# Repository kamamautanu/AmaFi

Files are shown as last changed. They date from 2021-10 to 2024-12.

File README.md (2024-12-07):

# AmaFi
Automated water-wise irrigation system

As someone new to the world of engineering, a friend encouraged me to create something that would make life easier for me. Something like automating watering in my garden so I don't spend 6 or more hours a week doing it by hand during the heat of summer. Initially, I resisted the idea of integrating technology into my gardening space, but as spring turned into summer and the hot California sun blasted my garden full force, what had once been a labor of love quickly turned into feelings of frustration at both the amount of time I spent watering and the amount of water I was using during a "mega-drought".

Water scarcity isn't an issue of the future, it's happening right here and now. Enter the AmaFi. The AmaFi only applies water where plants need it and when. No more worrying about over or under watering, the AmaFi takes out the guess work in growing drought resiliant gardens while conserving water compared to conventional methods. The AmaFi does this by integrating a number of gardening theories and features:
  * [deep watering]() - water less often for longer for deeper moisture penetration
  * [drip irrigation]() - reduces evapotranspiration, plant disease, and efficiently waters deeply
  * [irrigation zones] - three watering zones for crops based on rooting depth categories - low, medium, high.

# Table of Contents

  [What is AmaFi?](https://github.com/kamamautanu/AmaFi/blob/main/README.md#what-is-amafi)
  
  [What is next for AmaFi?](https://github.com/kamamautanu/AmaFi/blob/main/README.md#what-is-next-for-amafi)

Component Details
  1.  [Microprocessor](https://github.com/kamamautanu/AmaFi/blob/main/README.md#1-microprocessor)
  2.  [Case](https://github.com/kamamautanu/AmaFi/blob/main/README.md#2-case)
  3.  [Soil Moisture Sensor](https://github.com/kamamautanu/AmaFi/blob/main/README.md#3-soil-moisture-sensor)
  4.  [Relay](https://github.com/kamamautanu/AmaFi/blob/main/README.md#4-relay)
  5.  [Solenoid Valve](https://github.com/kamamautanu/AmaFi/blob/main/README.md#5-solenoid-valve)
  6.  [I2C Multiplexer](https://github.com/kamamautanu/AmaFi/blob/main/README.md#6-i2c-multiplexer)
  7.  [Other electrical components](https://github.com/kamamautanu/AmaFi/blob/main/README.md#7-other-electrical-components)
  8.  [Backflow Preventer](https://github.com/kamamautanu/AmaFi/blob/main/README.md#8-backflow-preventer)
  9.  [Water Pressure Regulator](https://github.com/kamamautanu/AmaFi/blob/main/README.md#9-water-pressure-regulator)
  10. [Water Filter](https://github.com/kamamautanu/AmaFi/blob/main/README.md#10-water-filter)
  11. [PVC Components](https://github.com/kamamautanu/AmaFi/blob/main/README.md#11-pvc-components)
  12. [Valves](https://github.com/kamamautanu/AmaFi/blob/main/README.md#12-valves)
  13. [Mainline](https://github.com/kamamautanu/AmaFi/blob/main/README.md#13-mainline)
  14. [Connecctors](https://github.com/kamamautanu/AmaFi/blob/main/README.md#14-Connectors)
  15. [Dripline](https://github.com/kamamautanu/AmaFi/blob/main/README.md#15-dripline)
  16. [Plugs and Caps](https://github.com/kamamautanu/AmaFi/blob/main/README.md#16-plugs-and-caps)
  17. [Other irrigation components](https://github.com/kamamautanu/AmaFi/blob/main/README.md#17-other-irrigation-components)  

[Bill of Materials (BOM)](https://github.com/kamamautanu/AmaFi/blob/main/README.md#bill-of-materials-BOM)

[Firmware](https://github.com/kamamautanu/AmaFi/blob/main/README.md#firmware)

[Schematic](https://github.com/kamamautanu/AmaFi/blob/main/README.md#schematic)

[User Manual](https://github.com/kamamautanu/AmaFi/blob/main/README.md#user-manual)

[FAQs](https://github.com/kamamautanu/AmaFi/blob/main/README.md#faqs)

[Tech Details](https://github.com/kamamautanu/AmaFi/blob/main/README.md#tech-details)

[Known Bugs](https://github.com/kamamautanu/AmaFi/blob/main/README.md#known-bugs)

[License](https://github.com/kamamautanu/AmaFi/blob/main/README.md#license)

# What is AmaFi?

I was inspired to create AmaFi to reduce the amount of time and water required by my garden. Ama, or more properly ᎠᎹ, is the Cherokee word for water and my watering system is powered by WiFi. How cool is that!

# What is next for AmaFi?

Four words - going solar and wireless. That's right, now that I have a functioning system up and running I can focus on making improvements. Check out some of my PCB designs in the making to improve the soil moisture sensors by trying to maximize parasitic capacitance. 

# Component Details

## 1. Microprocessor

The AmaFi uses the common microprocessor Raspberry Pi Zero W. It's compact, inexpensive, and has more than enough capacity and power for the AmaFi system.

Any Raspberry Pi requires a formatted microSD card and with hundreds of them on the market, the decision paralysis can set in quickly. The AmaFi is housed outdoors and while several weatherproofing techniques are used, the long-term performance of a microSD card is another critical factor in choosing one. With this in mind, I did some research to find a card with plenty of memory that was best for long-term performance and would perform *well enough* on the RasPi Zero W. My research led my to choose a 32GB Samsung Pro Endurance. It doesn't seem that anyone actually knows whether this microSD card lives up to the claims yet, but I figured it was worth a shot for starters. For more information about choosing a microSD for the RasPi, I found [this post](https://www.tomshardware.com/best-picks/raspberry-pi-microsd-cards) to be a good resource.

The microUSB port on the RasPi Zero W powers the system through a DC adapter plugged into a power outlet. Some of the other RasPi Zero W features utilized in this project are built in WiFi configured using headless setup, the I2C Interface, both the 3.3V and 5V power rails, digital pins that can be pulled high, among others.

## 2. Case

Since the electronic components of this system are located outdoors, thorough weatherproofing is especially imperative to the longevity of the device. With this in mind, a 3D enclosure was designed in OpenSCAD and Cura was used to convert the model into 3D printable g-code. The enclosure features 2 supports with zip tie slots, 2 internal pegs to mount 2 [half-sized Adafruit Permaboards](https://www.adafruit.com/product/571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), and a removable bottom that has 6 - 1/2 inch cylindrical cutouts for wires and a polygoon cutout for power adapters. The details for the AmaFi enclosure can be found [here](https://github.com/kamamautanu/AmaFi/tree/main/case). 

## 3. Soil Moisture Sensor

Soil moisture sensors use either resistive or capacitive sensing. Resistive sensors impute the volumentric content of water by measuring the current that passes through the soil between the two sensor prongs to get a resistance value. By design resistive sensors corrode quickly as current runs through the exposed soil probes causing electrolysis. On the other hand, capacitive sensing measures the dielectic formed by the soil and is actually a more accurate measure of soil moisture content compared to resistive sensing. Something like applying fertilizer would decrease the resistance sensor reading, but the most important factor influencing dielectic measurements taken by capacitance sensors is water. Capacitive sensors themselves are made out of a more corrossion resistive material, meaning they last longer than metal resistive sensors. I chose to go with the [Adafruit Capacitive Soil Moisture Sensor](https://www.adafruit.com/product/4026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). It runs on the I2C Bus, uses the MIT license, and comes with the added bonus of a temperature sensor that is accurate to +/- 2 degrees Celcius, which is good enough for my purposes.     

## 4. I2C Multiplexer

The Inter-Integrated Circuit (I2C) Interface on the Raspberry Pi allows multiple I2C devices to be connected to one I2C Bus as long as each device has a unique I2C address - multiple instances of the same address are not allowed. An I2C multiplexer allows multiple I2C sensors with the same I2C address to be connected to different channels on the multiplexer, thus allowing multiple sensors with the same I2C address to connect to one I2C Bus. One multiplexer was plenty for the 6 soil moisture sensors I needed to connect, but it is possible to implement more. I chose the [TCA9548A I2C Multiplexer](https://www.adafruit.com/product/2717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) from Adafruit.

## 5. Relay

In order to create three irrigation zones that operated and could be water idependently of one another, I had to utilize three relays. These relays run on digital GPIO pins that can be pulled high on the Raspberry Pi. Continuing the open source theme, I used the [Adafruit STEMMA Non-Latching Mini Relay](https://www.adafruit.com/product/4409).

## 6. Solenoid Valve

Assembled solenoid valves

Solenoid valves come in a variety of forms and sizes, but generally have two outlets for liquid and two terminals. I decided to go with the [Adafruit Plastic Solenoid Valve](https://www.adafruit.com/product/997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) as an inexpensive solution. It is a unidirectional liquid solenoid valve with two threaded 1/2" outlets and is powered by 12V DC. The solenoid valve is normally closed and opens when 12V DC current are applied to the valve terminals. Since my solenoid valves are installed downstream of the water pressure regulator I do not have concerns regarding their longevity. The gasket arrangement inside this particular solenoid valve requires a minimum pressure of 3 PSI for the solenoid valve to open. With a water pressure regulator of 25 PSI upstream, I'm not concerned about meeting the minimum pressure requirements. If the specifications in your system are different, make sure you meet the minimum pressure. If a hardier valve is needed, comparable metal ones can be implemented. These solenoid valves also come with a mesh filter built in, which is another bonus safeguard against damage to the drip system.

## 7. Other electrical components

In addition to the electrical components already covered, a number of other supplies are required to create an AmaFi:

* A soldering iron with a fine tip and solder are required. I'm not going to claim to be a soldering expert nor am I going to cover the topic in much detail here. There are plenty of great resources for learning online.

* Along with Multimeter, electrical tape, lots and lots of wires,
Let's talk more weatherproofing. The system has some built in weatherproofing of electical components with the 3D enclosure

## 8. Backflow Preventer

Backflow preventers do exactly that - they prevent water from flowing backwards and back into the main water supply, thus preventing potential contamination. There are metal and plastic backflow preventers to use depending on a system's unique requirements. Here, I decided to go for a [brass backflow preventer](https://www.dripdepot.com/product/aqualine-brass-three-quarter-inch-hose-end-vacuum-breaker).

## 9.  Water Pressure Regulator

In drip irrigation systems, water pressure regulators are essential for reducing water pressure to a level that the system can handle. Utilizing the correct water pressure for a drip system is important to assure that accurate volumes of water are applied and for the long-term longevity of the system. For most vegetable gardens and some other low-flow systems, a water pressure regulator that reduces water pressure to 25 PSI is adequate. I went with this [25 PSI Senninger 3/4" Hose Thread Pressure Regulator](https://www.dripdepot.com/item/senninger-three-quarter-inch-hose-thread-pressure-regulator-psi-25-psi).

## 10. Water Filter

The water filter in an irrigation system such as this acts as a safe guard against damage that the driplines could incur in a worst case scenario where particulate matter contaminates the main water supply. Since the dripline used in this systen have built in emitters, a [150 micron mesh filter](https://www.dripdepot.com/product/three-quarter-inch-hose-thread-filter) will do the job.

## 11. PVC Components

There are a number of ways to connect the main valve to the drip irrigation system. I wanted my system to be as sleek and sturdy as possible, so I decided to run PVC pipe to as close to my solenoids as I could. This involved digging an 18" deep, 12' long trench through hard clay soil from my main valve to my garden bed. I could have used a rotor tiller to do the hard labor for me, but I also wasn't sure where other pipes were, so I took the more cautious and laborious route. I happened to have more than enough 3/4" PVC pipe laying around from a previous irrigation project and the main valve that was already installed happened to be 3/4", so I stuck with this size for all of my PVC Components.

![]()

I found these cool [elbow](https://www.dripdepot.com/item/hydro-rain-pvc-lock-elbow-size-three-quarter-inch) and [tee](https://www.dripdepot.com/item/hydro-rain-pvc-lock-combination-tee-size-three-quarter-inch-pvcl-x-half-inch-fpt) PVC locks in the 3/4" size I needed for my PVC components that had a 1/2" female outlet to connect the solenoid valves, I also grabbed one of these [couplers](https://www.dripdepot.com/item/hydro-rain-pvc-lock-coupler-size-three-quarter-inch). These PVC components are great because you can just slide your PVC pipe in, give it a little tug, and you're good to go - no harsh solvents or waiting for things to dry and cure. Unfortunately, there were PVC components I needed that aren't available with Hydo-rain locks, so I also grabbed a [45 degree elbow](https://www.dripdepot.com/item/schedule-40-pvc-45-degree-slip-elbow-size-three-quarter-inch) and an [FPT PVC adapter](https://www.dripdepot.com/item/schedule-40-pvc-adapter-fpt-by-slip-slip-size-three-quarter-inch-fpt-size-three-quarter-inch), which are required in this set-up. PVC primer and cement are needed to secure the connections.

## 12. Valves

## 13. Mainline

The mainline is also known as the supply line because it feeds water from upstream to the driplines that are connected downstream making it a pillar in any drip irrigation system. Mainline can be made out of a number of materials, but I chose to go with polyethylene tubing because it is sturdy and cheap. Mainline also comes in a number of sizes from as small as 1/8" in diameter to over 1". The solenoid valves that I am using in my system are 1/2", so I went with a 1/2" diameter for my mainline as well. Before buying the mainline, I made sure that my system did not exceed the maximum run length or maximum gallons per hour supplied for the 1/2" polyethylene mainline tubing I intended to use - in this case 200' and 200 GPH, respectively. With around 25' of mainline, I can . Typically you would first calculate your run length and the GPH supplied to determine the size mainline your system required, but with the limiting factor in this scenario being the diameter of my solenoid valves

[1/2" Polyethylene Mainline](https://www.dripdepot.com/item/polyethylene-tubing-size-half-inch-600-inch-inside-diameter-by-700-inch-od-length-50-feet)

## 14. Connectors

[1/2" Threaded Perma-loc Tee Adapter](https://www.dripdepot.com/item/irritec-perma-loc-tubing-by-fpt-tee-adapter-perma-loc-size-half-inch-thread-size-half-inch-fpt)

[1/4" Barbed Tubing Couplers](https://www.dripdepot.com/item/barb-tubing-coupling-size-quarter-inch)

## 15. Dripline

Similar to mainline, dripline can be made from a number of materials in a range of sizes.

[1/4" Polyethylene Dripline](https://www.dripdepot.com/item/quarter-inch-polyethylene-dripline-emitter-spacing-6-inch-flow-rate-half-gph-roll-length-50-feet-color-black)

## 16. Plugs and Caps

[1/2" Perma-loc Cap](https://www.dripdepot.com/item/irritec-perma-loc-tubing-end-cap-perma-loc-size-half-inch)
[Goof Plugs](https://www.dripdepot.com/item/goof-plug-size-quarter-inch)

## 17. Other irrigation components

Additional materials that are required to build this drip irrigation system include: PVC primer and cement, plumber's tape, painter's tape

# Bill of Materials (BOM) 

| Ref | Item | pcs | Comment |
| --- | --- | ----- | --- |
| 1 | Raspberry Pi Zero W | 1 | |
| 2 | Samsung Pro 32 GB microSD card | 1 | |
| 3 | MicroUSB Power Supply | 1 | |
| 4 | Non-latching Mini Relay | 3 | |
| 5 | 1/2" 12V Plastic Solenoid Valve| 3 | |
| 6 | TCA9548A I2C Multiplexer | 1 | |
| 7 | Half-sized Permaboard | 2 | |
| 8 | Backflow Preventer | 1 | |
| 9 | Water Pressure Regulator | 1 | |
| 10  | 150 Micron Water Filter | 1 | |
| 11  | Capacitive Soil Moisture Sensor| 6 | |
| 12  | Samsung Pro 32 GB microSD card | 1 | |
| 14  | Raspberry Pi Zero W | 1 | |

Note: Complete this list.

# User Manual

## Getting started

  1. Download the appropriate version of [Raspberry Pi Imager](https://www.raspberrypi.com/software/) for your Operating System.

  2. Open Raspberry Pi Imager and insert the microSD card into the machine. Select the most current version of Raspberry Pi OS (Buster at the time of this writing), the microSD to burn the disk image to, and write the file - this could take a little bit of time.

  3. Configure headless setup on the RasPi and enable ssh. The documentation is [here](https://www.raspberrypi.com/documentation/computers/configuration.html#setting-up-a-headless-raspberry-pi).

  4. Plug the RasPi into the power supply and allow it to boot, this can take up to 5 minutes. If the previous steps were done correctly, the RasPi will automatically connect to the specified WiFi network at boot.

  5. To remotely connect to the RasPi using SSH, its IP address will need to be enumerated. There are a number of ways to do this, here the network scanning tool [nmap](https://nmap.org/download.html) is used. The following code can be used on the command line version of nmap or in the graphical user interface (GUI) of nmap, Zenmap:

  `nmap -sn YOURROUTERIP/24`

  6. SSH into the RasPi using the default credentials user:pi and password:raspberry and this line of code:

  `ssh -X pi@IPADDRESS`

  The -X option allows a program's GUI to be forwarded using ssh, it is required here to manually configure features on the RasPi.

  7. At login instructions to reset the password are given - change it to something secure and add the password to a password manager.

  8. Since the AmaFi system is programmed in CircuitPython, some initial setup is required for the RasPi. Update and install all the dependencies for CircuitPython, Seesaw, and the other Python modules. For an in depth guide to configuring CircuitPython on your RasPi, you can view the Adafruit documentation. Otherwise, here's the code I ran to configure my setup:

  `sudo apt-get update`

  `sudo apt-get upgrade`

  `sudo apt-get install python3-pip`

  `sudo pip3 install --upgrade setuptools`

  `sudo pip3 install --upgrade adafruit-python-shell`

  `wget https://raw.githubusercontent.com/adafruit/Raspberry-Pi-Installer-Scripts/master/raspi-blinka.py`

  `sudo python3 raspi-blinka.py`

  `sudo pip3 install adafruit-circuitpython-seesaw`

  `sudo pip3 install time`

  `sudo pip3 install `

 Note: Turn this into a script.

# FAQs

What's the science behind deep watering?

  When plants receive water more frequently in lower volumes, the water does not penetrate deeply into the soil, but the top layer of soil will be more moist more often. When this happens, plant roots are not encouraged to grow deeply into the soil and instead stay in the most shallow upper layer. When drought hits, these plants are not resilient and may suffer severe damage.

How do you encourage roots to grow deeply?

  By withholding water just long enough that crops enter the very initial stages of water stress, but not long enough to for irreversible damage to incur. This triggers the production of a hormone called Abscisic Acid (ABA). As ABA production increases it triggers roots to grow deeper into the soil to seek moisture. Increased root surface area in deeper parts of the soil ultimately makes plants more resilient to drought.

 What are the limitations of watering deeply?

 Heavy loam or clay soils can hold large volumes of water, but some soil types, namely sandy, drain too quickly and will require more frequent watering regardless. Adding organic mater to soil types like this can substantially increase the water holding capacity of the soil. Watering deeply is also not recommended when seeds or seedlings have yet to establish, as they won't be able to access water in the deeper soil layers.

 What type of irrigation system is best for watering deeply?

 If you ask me, drip irrigation all the way! Of course each type of system has unique requirements, but generally other types of irrigation systems, especially those involving overhead watering, apply water to the top soil level, usually at higher rates than the soil is able to absorb. This produces water waste in the form of runoff. In overhead irrigation systems, water is also lost in the form of evaporation, both off the surfaces of the soil and foliage. Overhead watering is also associated with an increase risk of disease in some plants as applying water to foliage often encourages bacterial and fungal growth. Drip irrigation does not water the top layer of soil in the same way. The trickling of water in this micro-irrigation system means that, when done correctly, water does not pool on the soil surface and instead is slowly absorbed into deeper layers of the soil over longer periods of time.   

# Known Bugs

* Occasionally when the watering program is ran, the following error is returned:

`Seesaw hardware ID returned (0xd5) is not correct! Expected 0x55. Please check wiring.`

  When this happens, CircuitPython is using the default Seesaw I2C address 0x55 instead of the address, 0x36, that has been specified in the program for soil moisture sensors. I'm not sure why this happens, but thankfully the error is mostly just an annoyance as it occurs infrequently and the watering program can simply be ran again. I still need to add error handling to for this edge case.

# License

The AmaFi device is licensed under Open-source hardware:
* Hardware is licensed under MIT
* Software is licensed under GNU
* Documentation is licensed under GNU.

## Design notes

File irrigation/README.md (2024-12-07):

# AmaFi Irrigation System

More than being an automated irrigation system, the goal of the AmaFi project is to conserve water using both conventional and novel approaches. There is far more research behind water conservation and irrigation techniques than can be covered here, so this section only covers the AmaFi irrigation system in greater detail.

Some of the main topics this sections covers are:

* [Water Conservation Methods]()
* [Installing the Irrigation System]()
* [Irrigation System Schedules]()

Note: Of course each garden and irrigation system has unique variables that accumulate to create a set of requirements. The components and design of the AmaFi irrigation system have only been tested in the context of this garden, but may work in others. Use with caution. 

## Water Conservation Methods

The AmaFi integrates these well known water conservation methods in addition to having some novel approaches:

**1. One simple way to improve soil moisture retention is by soil amendment**

  * **mulching** - adds organic matter to the top layer of soil, reduces the waste of water through evaporation in the top soil layer, untreated and undyed Redwood mulch is used here, which can help reduce soil alkalinity

  * **composting** - mixing organic matter into the soil is one of the best ways to improve soil moisture holding capacity and water retention while giving your plants a little bit of love in the form of fertilizer, compost was added to this system to improve the texture of the native heavy clay soil

**2. Deep watering**

Deep watering is a technique where the soil is saturated with water down to at least 6 to 8" below the soil surface. The system in return is not irrigated again until the soil is dry 6 to 8" below the soil surface. By withholding water just long enough that plants enter the very initial stages of water stress, but not long enough for irreversible damage to incur, roots are encouraged to grow deeper into the soil to seek moisture. The science behind this is simple - the production of a hormone called Abscisic Acid (ABA) is triggered in the initial stage of water stress and as ABA production increases it triggers roots to grow deeper into the soil. Increased root surface area in deeper parts of the soil ultimately makes plants more resilient to drought.

Many, if not most, conventional watering methods only saturate the soil to as deep as 6". Watering shallowly in this way means that roots are only encouraged to grow in the top soil layer. Compared to deep layers of the soil that do not experience irradiation from the sun, the top layer is heated which increases the evaporation of water. When drought hits, the top soil layer quickly dries, creating a problem as this is where the plant roots are located. Deep watering allows for growing drought-resilient plants in systems that use water more efficiently.

**3. Drip irrigation**

With deep watering as the theory behind the AmaFi irrigation system, drip irrigation is the technique that brings the theory functionality. When it comes to conventional irrigation techniques, drip irrigation is perhaps most well-known for its water conservation potential when applied in the appropriate context.

Other irrigation techniques can and usually do involve both overhead watering and saturating the entire soil surface with water. Both of these are problematic for different reasons. In overhead watering irrigation systems, water is lost in the form of evaporation, both off the surfaces of the soil and foliage. Overhead watering can also stress plants when the application timing is inappropriate and even increase the risk of disease by encouraging the growth of pathogenic fungi and bacteria. In contrast, when water is applied across the soil surface at rates higher than the soil can absorb, water is lost in the form of runoff waste. This means that not as much water is being absorbed into the system and the water that is stays in the top layer of soil, which we already know is susceptible to water loss through evapotranspiration.

Drip irrigation does not water the top layer of soil in the same way. The trickling of water in this micro-irrigation system allows water to be applied slowly enough that it is absorbed down into the root zone where we want it to encourage the growth of drough-resiliant plants instead of pooling at the surface.

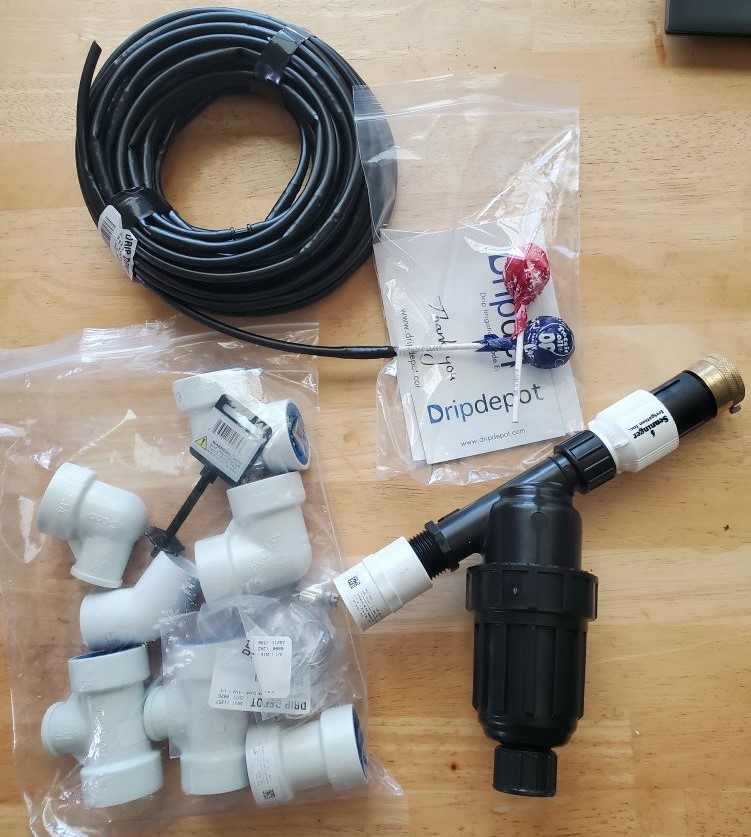
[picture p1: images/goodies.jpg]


## Installing the Irrigation System

The AmaFi irrigation system design is not particularly complicated, but following the assembly steps in the correct order during the installation process is important. I would recommend measuring and cutting the PVC pipe as you go and covering any exposed ends or terminals - plastic wrap and painter's tape are used here. The following is the recommended order of assembly for the irrigation system:

  1. Install the capped polyethylene mainlines and attach these to the tee solenoid valve adapters.

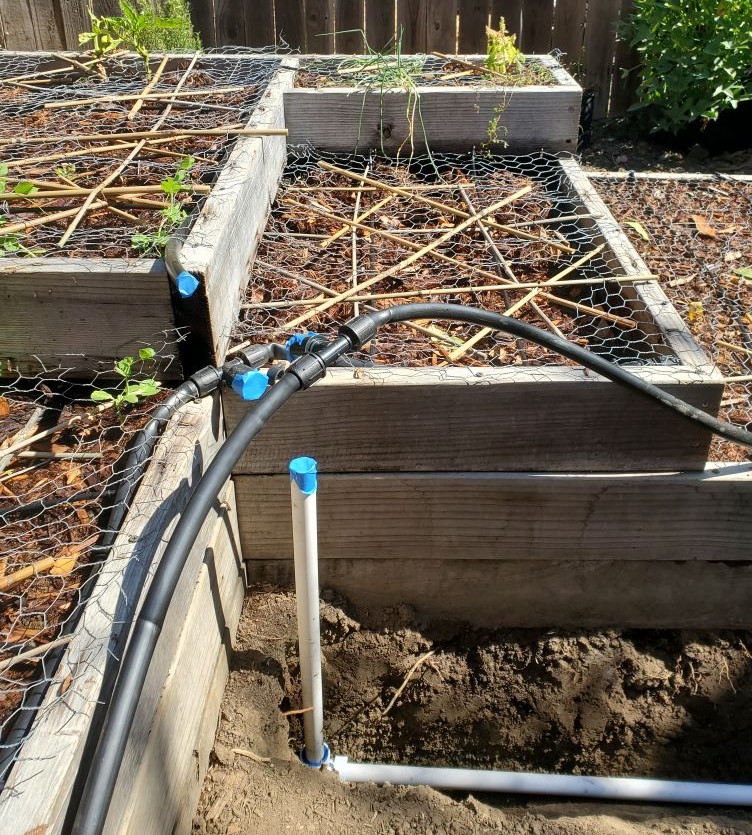
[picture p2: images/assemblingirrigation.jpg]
  

  2. Dig or rotor till an 18" deep trench from the main valve to the garden bed.

  3. Using threaded sealant tape, wrap all the threaded components making sure to go in the direction of the threads several times, and connect the threaded irrigation components.

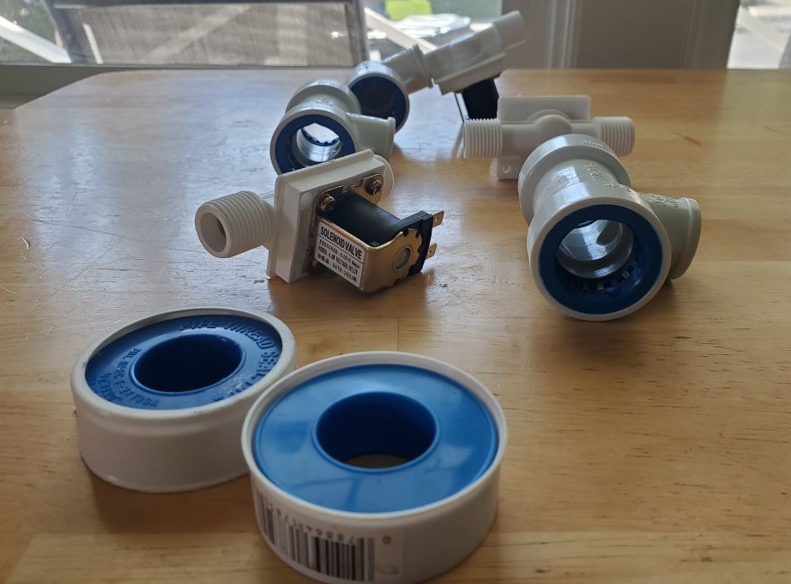
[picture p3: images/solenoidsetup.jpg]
  

  4. Thread the solenoids to the PVC tee and elbow adapters.

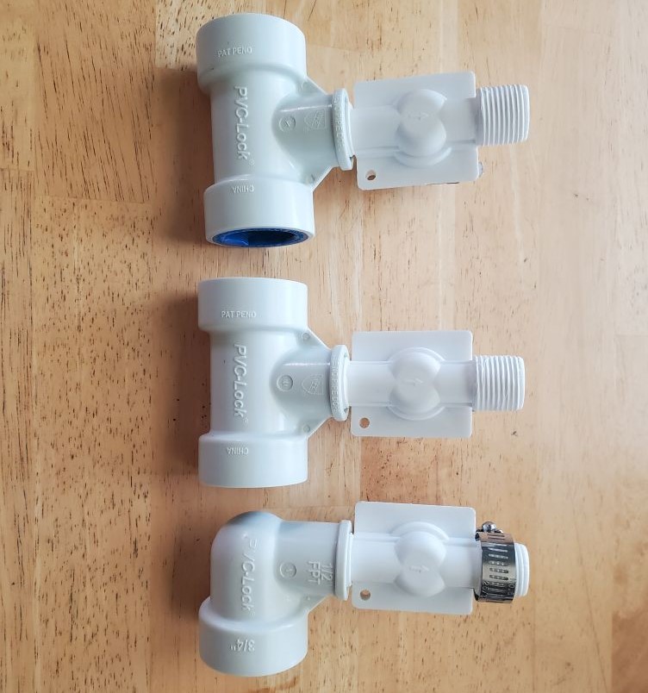
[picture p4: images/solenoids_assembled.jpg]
  

  5. Thread the solenoid and PVC pipe adapters to the mainline adapters.

  6. Working downstream, lock PVC pipe between solenoid adapters.

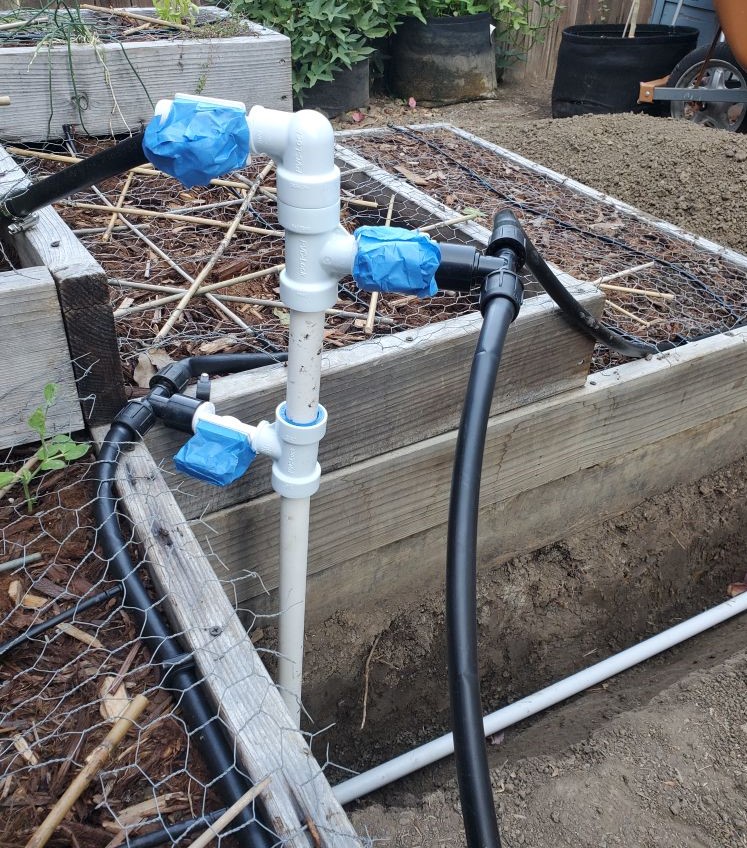
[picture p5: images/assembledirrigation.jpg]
  

  7. To seal the regular Schedule 40 PVC components upstream, thoroughly prime the joints and apply cement.

  8. Assemble primed and cemented PVC components and allow to dry and cure.

  9. Start to backfill the trench with small rocks, gravel, or soil chunks to help keep the pipe in place.

  10. Finish backfilling the trench and smooth over the surface, periodically checking to make sure the aboveground PVC components are still in place and adjusting accordingly.

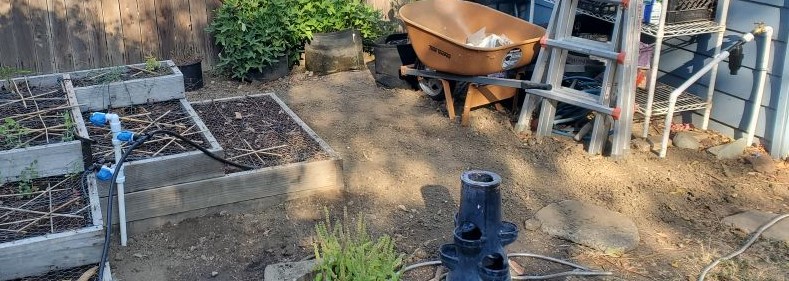
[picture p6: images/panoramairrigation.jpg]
  

  11. Walk over the area to slightly compact the soil.

## Irrigation Schedule Programs

The AmaFi uses irrigation schedule programs developed in CircuitPython. If you possess the time and skills, you can program your own irrigation schedule for your device. Otherwise the following executable programs can be downloaded onto your AmaFi:

* [seedlings.py]() - applies less water more often, intended for seeds and seedlings
* [watering.py]() -
* [envmonitor.py]() - 
* [compost.py]() - 
* You can schedule this as a cron job - I recommend early morning

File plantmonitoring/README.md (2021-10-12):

# AmaFi Plant Monitoring System

Currently, the AmaFi plant monitoring system has these features:
  * Capacitive soil moisture and ambient temperature sensors for 5 garden beds in 3 irrigation zones
  * Custom length 4-pin JST connectors for I2C sensors
  * Multiplexer to connect multiple I2C sensors with the same address
  * Lower power consumption than the irrigation system through the 3.3V power rail on the RasPi
  * Automated data management using SQL Alchemy to interface with an SQLite database in Python
  * Weatherproofing with heat shrink, conduit, and conformal coating

# database

There are a number of open-source database engines available for managing data, but for the Raspberry Pi something lightweight is preferred.

SQLite features"
* Preinstalled with Python3 so no additional configuration
* Lightweight
*
*

 is used here because it is lightweight and comes with Python 3. Another appealing feature of SQLite is that it can store data in-memory, meaning a database server does not have to be used. Rather than using SQL to communicate with the database, an Object Relational Model (ORM) is implemented with SQLAlchemy in Python. This allows for communication with the database by treating the SQL queries on the database as Python objects. Since the database is in-memory, an ORM is a good fit as a server isn't involved to slow down data management process. There are several ways to create an ORM

First, install SQLAlchemy:

  `sudo pip3 install sqlalchemy`

Next, set-

By strategically placing soil moisture sensors

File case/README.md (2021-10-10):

# AmaFi Enclosure

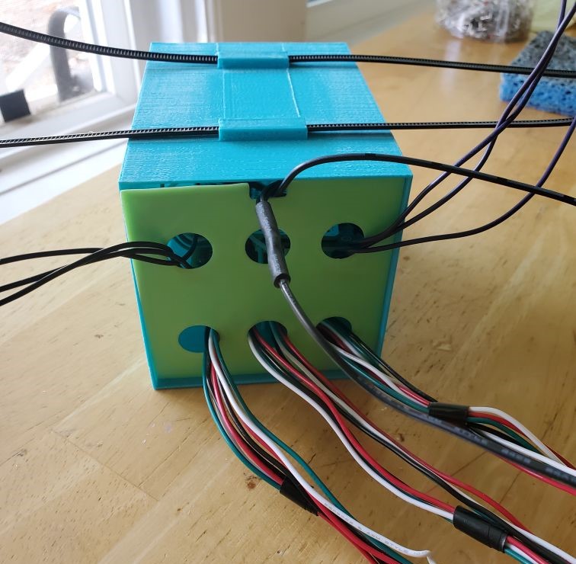
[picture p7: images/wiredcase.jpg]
Assembled Case


The AmaFi enclosure is designed using parametric 3D modeling techniques in [OpenSCAD](https://openscad.org/downloads.html) and converted to g-code using [Cura](https://ultimaker.com/software/ultimaker-cura).

The OpenSCAD files for the [case](https://github.com/kamamautanu/AmaFi/blob/main/case/case.scad) and [bottom cover](https://github.com/kamamautanu/AmaFi/blob/main/case/bottom.scad) can be downloaded and modified directly. The step files for the 3D models can also be downloaded directly and printed with a 3D printer:

  * [case.stl](https://github.com/kamamautanu/AmaFi/blob/main/case/case.stl) - this is the main compartment that features pegs for mounting Permaboards and supports with 2 zip tie slots

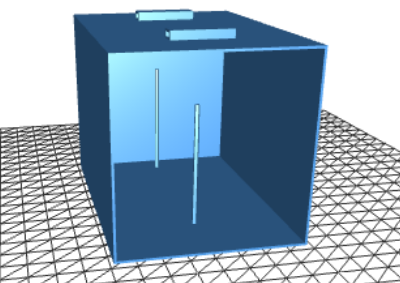
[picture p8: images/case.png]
Internal view of the AmaFi case
  

  * [bottom.stl](https://github.com/kamamautanu/AmaFi/blob/main/case/bottom.stl) - this is a cover that slides into the bottom of the case that features 6 - 1/2" circle cutouts to feed the sensor, solenoid, and power wiring through. A few different designs were tried before settling on this one

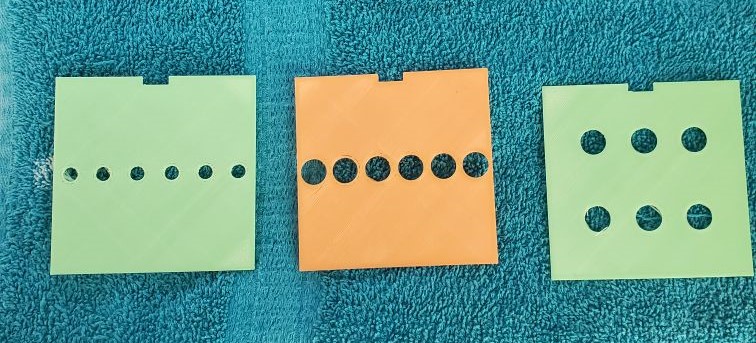
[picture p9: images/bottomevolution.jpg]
Evolution of the bottom cover design for the AmaFi case
  

Here are a few pointers to successfully print these 3D models:

  * In 3D software, use a raft to increase adhesion of the PLA filament to the printing platform on the 3D printer

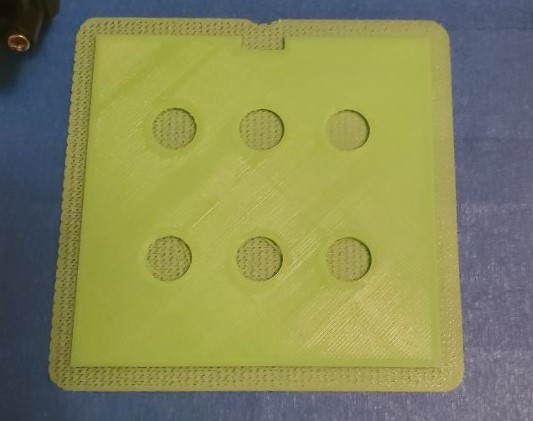
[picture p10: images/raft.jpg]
Example raft on bottom cover
      

  * Also configure the case to be printed with supports everywhere to provide stability to the final product

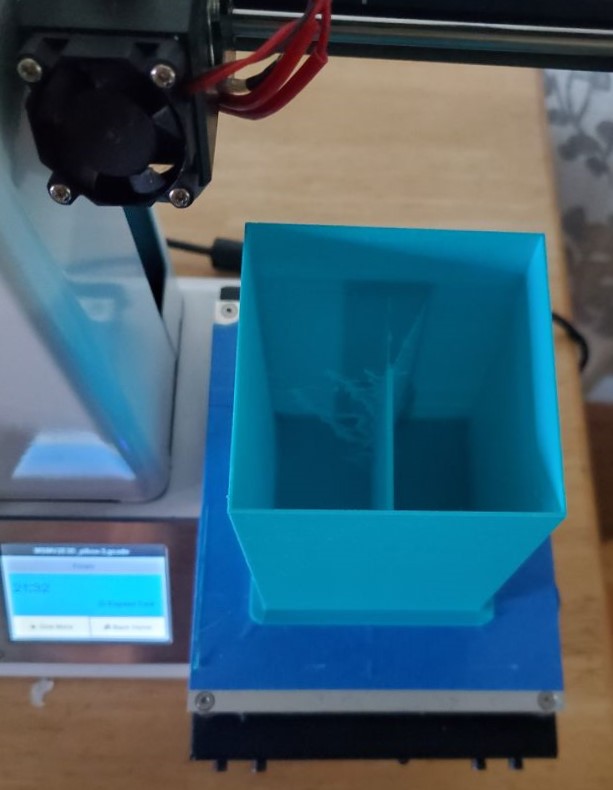
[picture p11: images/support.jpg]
Example case printed with supports everywhere
      

  * Depending on the 3D printer, the case will probably need to be rotated around in the 3D software to fit inside the printing area
  * Print the walls of the case and the bottom cover at least 2 mm thick, preferably more if you can manage
  * Sand the exterior walls of the product and apply a UV proofing solvent if using PLA filament as it is not UV resistant

   **Note:** Increasing the thickness of the AmaFi enclosure and adding adapters for conduit on the bottom cover will be the main objective of future revisions.

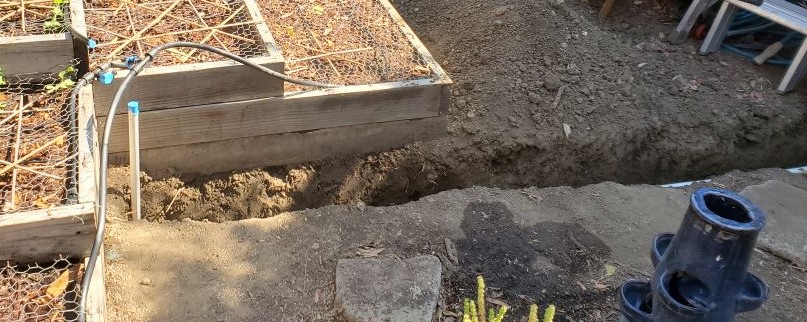
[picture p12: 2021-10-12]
images/trenchedirrigation.jpg

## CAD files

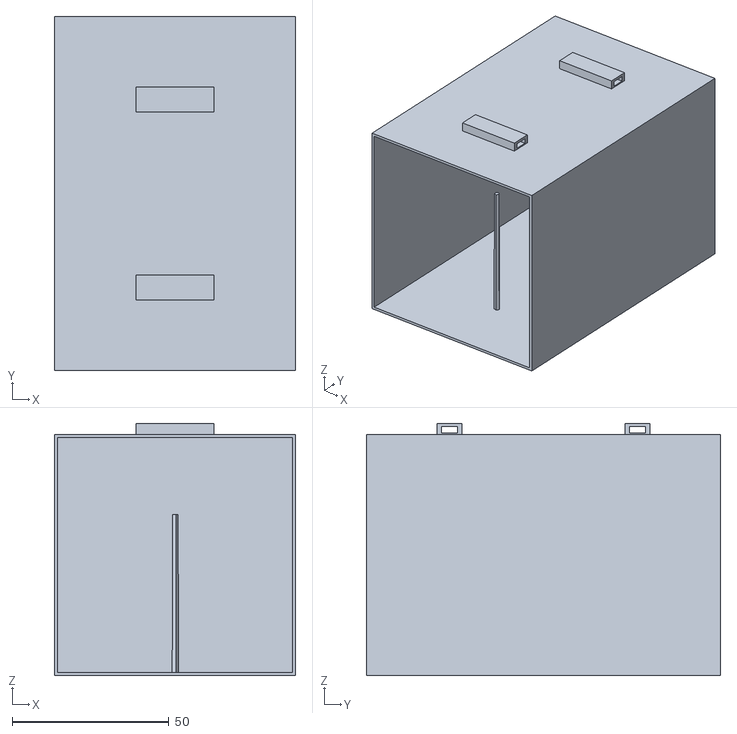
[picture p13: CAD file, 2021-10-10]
case/case.stl
77.0 x 113.0 x 80.5

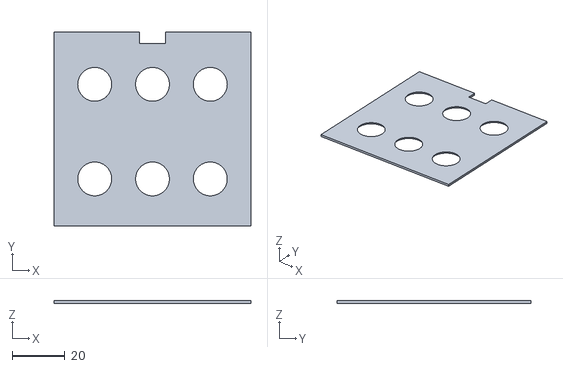
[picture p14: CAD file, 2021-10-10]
case/bottom.stl
75.0 x 74.0 x 1.00

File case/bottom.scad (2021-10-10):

//AmaFi Bottom Cover

//Set variables (mm):
//Cover
bcx = 75; //cover width
bcy = 74; //cover height
bcz = 1; //cover thickness
// Power witing cutouts
lcx = 10; //
lcy = 5; //
lcz = 5; //
lct = [0,35,0]; //cutout trans
//Wiring cutouts
h = 20; //cutout height
d = 12.5; //cutout diameter
cy1t = 17; //row 1 translation
cy2t = -19; //row 2 translation
czt = 0; //z translation
cx1t = -22; //column 1 trans
cx2t = 0; //column 2 translation
cx3t = 22; //column 3 translation

//Create cover:
difference() { //remove cutouts
cube([bcx,bcy,bcz], center = true);
//polygon cutout
translate(lct)
cube([lcx,lcy,lcz], center = true);
//top-left cutout
translate([cx1t,cy1t,czt])
cylinder(h, d, center = true);
//bottom-left cutout
translate([cx1t,cy2t,czt])
cylinder(h, d, center = true);
//top-middle cutout
translate([cx2t,cy1t,czt])
cylinder(h, d, center = true);
//bottom-middle cutout
translate([cx2t,cy2t,czt])
cylinder(h, d, center = true);
//top-right cutout
translate([cx3t,cy1t,czt])
cylinder(h, d, center = true);
//bottom-right cutout
translate([cx3t,cy2t,czt])
cylinder(h, d, center = true);    
}

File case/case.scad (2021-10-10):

//AmaFi Weatherproofing Case

//Set variables (mm):
//Case
h = 113; //height
l = 77; //length
w = 76; //width
t = 1; //thickness
ht = (0.5*h); //h translation
lt = (0.5*l); //l translation
wt = (0.5*w); //w translation
//Pegs
ch = 51; //cylinder height
cr = 1.1; //cylinder radius
tcyt = 45 ; //top peg y trans 
bcyt = tcyt - 73.7; //bottom peg y translation
//Supports and zip tie slots
bh =25; // polygon height
b1l = 8; //polygon length
b1w = 4; //polygon width
b2l = 5; //cutout length
b2w = 2; //cutout width
bxt = 0; //x translation
byt = 30; //y translation
bzt = 40; //z translation

//Create Case:
//front side 
translate([0,0,-wt])
   cube([l,h,t], center = true);
//back side
translate([0,0,wt])
   cube([l,h,t], center = true);
//left side
translate([wt,0,0])
   cube([t,h,w], center = true);
//right side
translate([-wt,0,0])
   cube([t,h,w], center = true);   
//top side
translate([0,ht-0.5,0])
   cube([l,t,w], center = true);
   
//Create mounting pegs:
//top peg
translate([0,tcyt,-wt])
    cylinder(ch,cr);
//bottom peg
translate([0,bcyt,-wt])
    cylinder(ch,cr);

//Create supports
difference()  {    
translate([bxt,byt,bzt])
   cube([bh,b1l,b1w], center = true); //top slot
translate ([bxt,byt,bzt]) 
   cube([bh,b2l,b2w], center = true); //remove cutout  
    }   
difference()  {    
translate([bxt,-byt,bzt])
   cube([bh,b1l,b1w], center = true); //bottom slot
translate ([bxt,-byt,bzt]) 
   cube([bh,b2l,b2w], center = true); //remove cutout   
    }

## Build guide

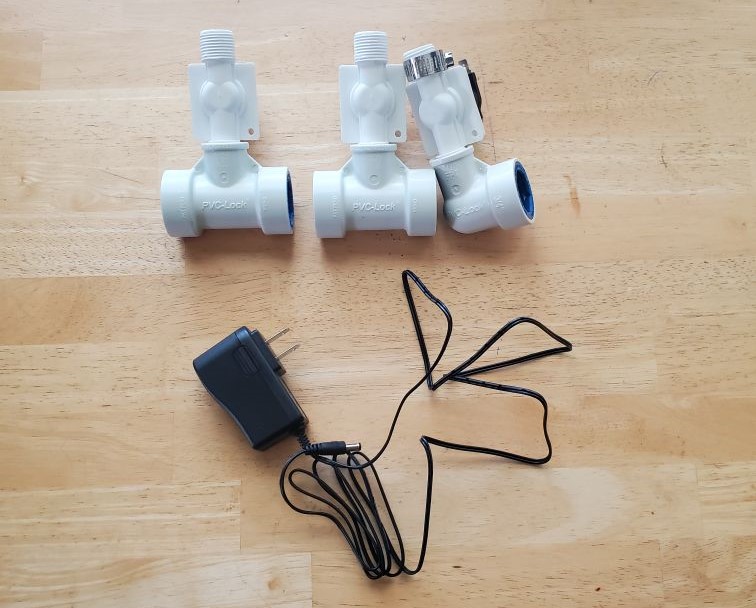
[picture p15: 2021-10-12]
images/assembledsolenoids.jpg

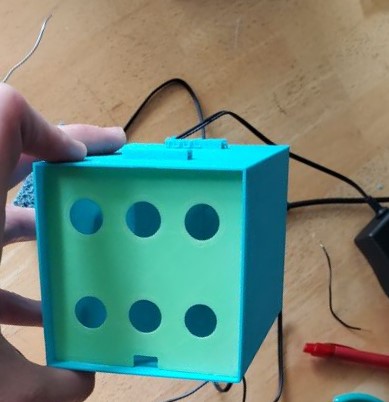
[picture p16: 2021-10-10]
images/assembledcase.jpg

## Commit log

2021-10-10 Commit STL 3D Model for bottom lid to case folder
    [bottom.stl]
2021-10-10 Commit STL 3D models for the case and bottom cover
    [bottom.stl, case.stl]
2021-10-10 Commit JPG images of case to new images folder
2021-10-10 Set up README.md for case and test links
2021-10-10 Commit OpenSCAD models for case and bottom cover
    [bottom.scad, case.scad]
2021-10-10 Add comments to SCAD 3D models
    [bottom.scad, case.scad]
2021-10-10 Update AmaFi Case folder
    [case.stl]
